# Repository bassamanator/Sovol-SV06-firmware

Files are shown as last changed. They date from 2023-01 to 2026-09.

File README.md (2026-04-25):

<p align="center">
Please consider
<a href="https://ko-fi.com/bassamanator" target="_blank">donating</a> to
support my open source work ❤️
</p>

# One-Stop-Shop Klipper Configuration

| Printer | Branch |
| --- | --- |
| ${\normalsize{\textcolor{darkturquoise}{\text{Sovol SV06}}}}$ | ⚡ ${\scriptsize{\textcolor{darkturquoise}{\text{YOU ARE HERE}}}}$ ⚡ |
| Sovol SV06 SKR-Mini-E3-V3.0 | [skr-mini-e3-v3](https://github.com/bassamanator/Sovol-SV06-firmware/tree/skr-mini-e3-v3) |
| Sovol SV06 Fly-E3-Pro-V3 | [fly-e3-pro-v3](https://github.com/ElPainis/Fly-E3-Pro-v3) \*\* |
| Sovol SV06 Plus | [sv06-plus](https://github.com/bassamanator/Sovol-SV06-firmware/tree/sv06-plus) |
| All other printers | [any-printer](https://github.com/bassamanator/Sovol-SV06-firmware/tree/any-printer) |

${\small{\textit{** Maintained by ElPainis}}}$

> [!WARNING]
> I am creating these files for my personal use and cannot be held responsible for what it might do to your printer. Use at your own risk.

## Outline

- [Features](#features)
- [Stay Up-to-Date](#stay-up-to-date)
- [Preface](#preface)
- [Before You Begin](#before-you-begin)
- [Klipper Installation](#klipper-installation)
  - [Flash Firmware](#flash-firmware)
  - [Download OSS Klipper Configuration](#download-oss-klipper-configuration)
- [Initial Steps](#initial-steps)
  1. [Adjust Configuration with MCU Path](#adjust-configuration-with-mcu-path)
  2. [Configure Your Printer](#configure-your-printer)
- [Adjust Your Slicer](#adjust-your-slicer)
- [Support Me](#support-me)
- [Directory Structure](#directory-structure)
- [Special Considerations](#special-considerations)
- [FAQ](#faq)
- [Useful Resources](#useful-resources)
- [Sovol Official Links](#sovol-official-links)
- [Sources](#sources)

## Features

- 💥 This Klipper configuration is an _endpoint_, meaning that it contains **everything** that you could possibly need in order to have an excellent Klipper experience! 💥
- Filament runout sensor usage implemented.
- Minimum configuration settings for `Mainsail` and `Fluidd`.
- Pre-configured configuration bundles based on the [Ellis SuperSlicer Print Profiles](https://github.com/AndrewEllis93/Ellis-SuperSlicer-Profiles):
  - SuperSlicer
  - PrusaSlicer
  - 🚀 OrcaSlicer 🚀
  - Printer profiles: `SV06/Plus`; `SV07/Plus`
- Bed model and texture to use in SuperSlicer/PrusaSlicer.
- Macros:
  - **Improved** mechanical gantry calibration/`G34` macro that provides the user audio feedback, and time to check the calibration.
  - Misc macros: `PRINT_START`, `CANCEL_PRINT`, `PRINT_END`, `PAUSE`, `RESUME`.
  - Parking macros (parks the printhead at various locations): `PARKFRONT`, `PARKFRONTLOW`, `PARKREAR`, `PARKCENTER`, `PARKBED`.
  - Load/unload filament macros.
  - `PURGE_LINE` macro.
  - `TEST_SPEED` macro. Find instructions [here](#how-do-i-use-the-test_speed-macro).
- Klipper Adaptive Meshing & Purging (KAMP) integrated. Read about it [here](#what-do-i-need-to-know-about-kamp).

[🔼 Back to top](#outline)

## Stay Up-to-Date

${\normalsize{\textcolor{goldenrod}{\texttt{Star ⭐ this project.}}}}$

Watch for [updates](https://github.com/bassamanator/Sovol-SV06-firmware/discussions/37).

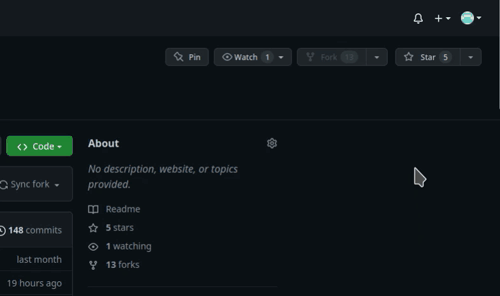
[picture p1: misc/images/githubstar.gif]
github star


[🔼 Back to top](#outline)

## Preface

Although I've made switching over to Klipper as easy as is possible, it can still be a challenge for some, especially considering that most of you have likely never used GNU+Linux. Save yourself the frustration, and fully read this documentation. Also note that Klipper is not a _must_, and is not for everyone. You can stick with Marlin, and have a fine 3D printing experience.

In many ways, this entire repository can be considered _my opinion_ on the `3D printing experience` and this has been _my attempt_ to share that experience. Some factors, such as _accuracy_ and _testing_, have been at the forefront of my thoughts during this process. I hope you find this repository suitable. Cheers.

[🔼 Back to top](#outline)

## Before You Begin

- This entire page is a **9 minute read**. Save yourself _hours of troubleshooting_ and read this documentation fully.
- Follow the steps in order. If an error was reported at a step, do no proceed to the next step.
- It is assumed that you are connected to your host Raspberry Pi (or other host device) via SSH, and that your printer motherboard is connected to the host via a _data_ USB cable.
- It is also assumed that the username on the host device is `pi`. If that is not the case, edit `moonraker.conf` and `cfgs/misc-macros.cfg` to change any mentions of `/home/pi` to `/home/yourUserName`.
- Klipper _must_ be installed on the host beforehand. Easiest is to use [MainsailOS](https://github.com/mainsail-crew/mainsail/releases/latest). [KIAUH](https://github.com/th33xitus/kiauh) is another option.
- Klipper _must_ be up to date.
  - In `Fluidd`, you can do this from `Settings` > `Software Updates`.
  - In `Mainsail`, you can do this from `Machine` > `Update Manager`.
- Robert Redford's performance in _Spy Game (2001)_ was superb!
- It is assumed that there is one instance of Klipper installed. If that is not the case, the steps in this guide will not work _perfectly_ for you.
- Your question has probably been answered already, but if it hasn't, please post in the [Discussion](https://github.com/bassamanator/Sovol-SV06-firmware/discussions) section.
- I would recommend searching for the word `NOTE` in this configuration. There are roughly half a dozen short points amongst the various files that you should be aware of.
- Consider [these](https://github.com/bassamanator/everything-sovol-sv06/blob/main/parts/README.md#printed-upgrades) printable parts, and also see my [Printables](https://www.printables.com/@bassamanator) page.

> [!TIP]
> Most of the micro USB cables that you find at home are _unlikely_ to be data cables, and it is not possible to tell just by looking.

> [!CAUTION]
> Make sure your printer is in good physical condition, because print and travel speeds will be _a lot faster_. Beginners would be wise to run through [these steps](https://github.com/bassamanator/everything-sovol-sv06/blob/main/initialsteps.md).

> [!CAUTION]
> [Disable](https://github.com/bassamanator/everything-sovol-sv06/blob/main/howto.md#disable-usb-cable-5v-pin) the USB cable's 5V pin.

[🔼 Back to top](#outline)

## Klipper Installation

### Flash Firmware

💡 If you flashed Klipper onto your motherboard in the past, you can skip this step.

Please note:

- For the sake of simplicity, I will refer to the firmware file as `klipper.bin` even though the actual filename is something along the lines of `klipper-v0.11.0-148-g52f4e20c.bin`.
- The firmware file is located in the `misc` folder.
- Flashing will only work if current firmware filename is _different from previous flashing procedure_. The `.bin` is also important.
- You may find this [video](https://youtu.be/p6l253OJa34) useful.

> [!WARNING]
> Many users have reported having issues flashing Klipper using the Sovol microSD card.

#### 1. Prepare the microSD Card for Flashing with These Parameters

- Size: `16GB` maximum.
- File system: `FAT32`.
- Allocation unit size: `4096 bytes`.
- Must not contain any files _except_ the firmware file.

#### 2. Flashing Procedure

1. Disconnect any USB cables that might be connected to the motherboard.
2. Copy `klipper.bin` to the microSD card.
3. Make sure the printer is off.
4. Insert the microSD card into printer.
5. Turn on the printer and wait a minute (usually takes 10 seconds).
6. Turn off the printer and remove the microSD.

> [!IMPORTANT]
> ⏲️ At this point, it's not possible to tell with certainty whether your flash was successful, continue on with the guide.

[🔼 Back to top](#outline)

### Download OSS Klipper Configuration

#### Method 1: Clone the Repository

💡 Make sure `git` is installed (`sudo apt update && sudo apt install git`).

1. `ssh` into the Klipper host.
2. `cd ~/printer_data/config`
3. Empty entire `~/printer_data/config` folder.
   - In linux, you can delete files via `rm fileName` and directories via `rmdir directoryName`.
   - In linux, you can list files and folders via `ls -lah`.
4. `git clone -b master --single-branch https://github.com/bassamanator/Sovol-SV06-firmware.git .` ⚠️ Don't miss the period!

#### Method 2: Download the ZIP

1. [Download](https://github.com/bassamanator/Sovol-SV06-firmware/archive/refs/heads/master.zip) the `ZIP` file containing the Klipper configuration.
2. See `Step 2` in `Method 1`.
3. The parent folder in the `ZIP` is `Sovol-SV06-firmware-master`. This is relevant in the next step.
4. Extract **only** the _contents_ of the parent folder into `~/printer_data/config`.

[🔼 Back to top](#outline)

## Initial Steps

### Adjust Configuration with MCU Path

💡 Make sure the host and printer are connected via USB.

1. Find what port the `mcu` (printer motherboard) is connected to via _one_ of the following commands:

   - `ls /dev/serial/by-id/*`
   - `ls /dev/serial/by-path/*`

   1. The output will be something along the lines of
      - `/dev/serial/by-id/usb-1a86_USB2.0-Serial-if00-port0`

2. Adjust the `[mcu]` section in `printer.cfg` accordingly.

   ```yaml
   # 📝 This is just an example
   [mcu]
   serial: /dev/serial/by-id/usb-1a86_USB2.0-Serial-if00-port0
   restart_method: command
   ```

3. Do a `FIRMWARE_RESTART` in the Klipper console.

If the Klipper flash that you did earlier was successful, and you've done everything else correctly, you should see no errors or warnings in the `Mainsail`/`Fluidd` dashboard. 🎉 **Your printer has been Klipperized!** 🎉

[🔼 Back to top](#outline)

### Configure Your Printer

❗☠️ **Your finger should be on the power switch for most of these steps** ☠️❗

❗☠️ **Power off if there is a collision/problem** ☠️❗

💡 The ${\small{\textcolor{red}{\texttt{EMERGENCY STOP}}}}$ button in your dashboard works faster than hitting the power switch.

💡 Do a practice emergency stop.

💡 I recommend no filament be loaded for any of these steps.

> [!NOTE]
> You will be pasting/typing these commands into the `Mainsail`/`Fluidd` console.

1. Check to see if `X` and `Y` max positions can be reached, and adjust `position_max`, if necessary. You might be able to go further, which is great, but I recommend leaving a 2mm gap for safety.
   1. `G28`
   2. `G90`
   3. `G1 X223 F3000`
   4. `G1 Y223 F3000`
2. Do a mechanical gantry calibration; `G34`. After the controlled collision against the beam at the top, there will be a 10 second pause for you to verify that both sides of the gantry are pressed up against the `stoppers` at the top. You will hear a succession of beeps.
   1. Figure out your `Z` `position_max` by baby stepping your way up to the beam, and adjust `position_max`, if necessary.
3. PID tune the bed. Ideally, all PID tuning should occur at the temperatures that you print most at.
   1. `PID_TEST_BED TEMP=70`
   2. `SAVE_CONFIG` (once completed)
4. PID tune the extruder while part cooling fan runs at 25%.
   1. `PID_TEST_HOTEND TEMP=245`
   2. `SAVE_CONFIG` (once completed)
5. Adjust `z_offset`. Make sure your nozzle if very clean. Do the [Paper test](https://www.klipper3d.org/Bed_Level.html?h=probe_calibrate#the-paper-test).
   1. `DO_PROBE_CALIBRATE`
   2. Follow `z_offset` setup in `Mainsail`/`Fluidd`.
   3. `SAVE_CONFIG` (once completed)
6. Create a bed mesh.
   1. `DO_CREATE_MESH`
   2. `SAVE_CONFIG` (once completed)

🏁 If you've made it here, then your Klipperized printer is ready to print! 🏁

_But first_, adjust your slicer.

[🔼 Back to top](#outline)

## Adjust Your Slicer

> [!NOTE]
> If you are using the slicer bundles found on this repo, you can skip this section.

### Start G-Code

It varies depending on your slicer. Find instructions [here](https://ellis3dp.com/Print-Tuning-Guide/articles/passing_slicer_variables.html#slicer-start-g-code).

### End G-Code

```
PRINT_END
```

### Line Purge

If you would like to print a purge line before your print starts, at the end of your start gcode, on a new line, add one of the following:

- `PURGE_LINE`; prints a standard purge line.
- `KAMP_LINE_PURGE`; prints KAMP's purge line.

> [!WARNING]
> Do not attempt to use `KAMP_LINE_PURGE` without reading [this section](#what-do-i-need-to-know-about-kamp).

```yaml
# 📝 This is just an example Start G-Code
PRINT_START ...
PURGE_LINE
```

[🔼 Back to top](#outline)

## Support Me

Please ⭐ star this repository!

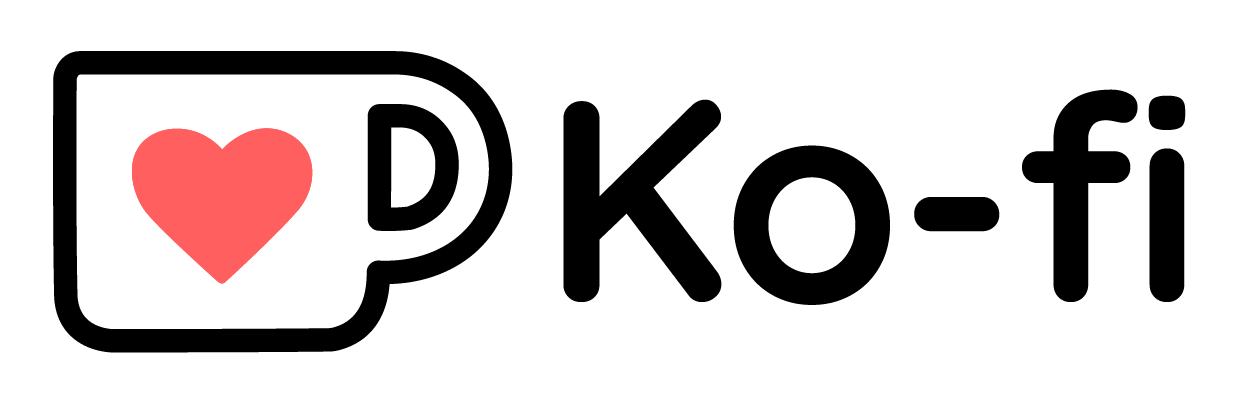
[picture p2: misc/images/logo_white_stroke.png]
Ko-fi
Support [open source](https://en.wikipedia.org/wiki/Open_source), and buy me a [](https://ko-fi.com/bassamanator).

[🔼 Back to top](#outline)

## Directory Structure

This repository contains many files and folders. Some are _necessary_ for this Klipper configuration to work, others are not.

- **Necessary** items are marked with a ✅.
- Items that can _optionally_ be deleted are marked with a 💠.
<!-- tree -a -C -I '.directory' -L 1 -F -->

```sh
/home/pi/printer_data/config
├── cfgs/ ✅
├── CODE_OF_CONDUCT.md 💠
├── CONTRIBUTING.md 💠
├── .git/ ✅❔
├── .github/ 💠
├── .gitignore ✅❔
├── LICENSE 💠
├── misc/ 💠
├── moonraker.conf ✅
├── osskc.cfg ✅
├── printer.cfg ✅
├── README.md 💠
├── SECURITY.md 💠
└── .vscode/ 💠
```

[🔼 Back to top](#outline)

## Special Considerations

### Sequential printing

If enabled, cancelling, or resuming a print from pause, could lead to collisions with previously printed objects. In order to prevent collisions, in your slicer, ensure that objects are printed from the back of the build plate to the front.

In PrusaSlicer, please see Printer Settings > Notes, for extruder clearances.

### Errors

#### MCU 'mcu' shutdown: Timer too close

This error often occurs when the `mcu` is unable to generate the required `microsteps`. Lower power Klipper hosts might be especially susceptible. Reducing `microsteps` to `64`, or even `32` can resolve the issue.

[🔼 Back to top](#outline)

## FAQ

### What are some settings that I can change?

Edit the relevant file according to your needs.

| File | Section |
| --- | --- |
| `cfgs/misc-macros.cfg` | `[gcode_macro _globals]` |

| Variable | Disable | Enable | Notes |
| --- | --- | --- | --- |
| `variable_beeping_enabled` | `0` | `1` (default)  |
| `variable_filament_sensor_enabled` | `0` (default) | `1` |
| `variable_kamp_enable` | `0` (default) | `1` | See [here](#what-do-i-need-to-know-about-kamp) |
| `variable_bed_temp_over` | `0` | `10` (default) | Speeds up print start |
| `variable_bed_temp_not_exact` | `0` | `1` (default)  | Speeds up print start |

### Any differences between this configuration and Sovol's Marlin firmware?

| Property | Marlin | OSS Klipper Config |
| --- | --- | --- |
| `stepper_z` `run_current` | 0.800  | 0.900 |
| `microsteps` | 16 | 128 |

### How do I import a configuration bundle into SuperSlicer/PrusaSlicer?

Please see this [discussion](https://github.com/bassamanator/Sovol-SV06-firmware/discussions/13).

### How do I print using SuperSlicer/PrusaSlicer?

Please see this [discussion](https://github.com/bassamanator/Sovol-SV06-firmware/discussions/14).

### When does beeping occur?

The printer will beep upon:

- Filament runout.
- Filament change/`M600`.
- Upon `PRINT_END`.
- `MECHANICAL_GANTRY_CALIBRATION`/`G34`.

### I want to use a filament sensor. How do I set it up?

You can find information about the physical setup [here](https://github.com/bassamanator/everything-sovol-sv06#filament-sensor).

You can test the sensor via `QUERY_FILAMENT_SENSOR SENSOR=filament_sensor`.

### My filament runout sensor works, but I just started a print without any filament loaded. What gives?

A simple runout sensor can only detect a change in state. So, if you start a print without filament loaded, the printer will not know that there is no filament loaded. You should test your sensor by having filament loaded, starting a print, then cutting the filament. The expected behaviour is that the print will pause, and as long as you have beeping enabled, you will hear 3 annoying beeps.

### What happens when I put in `M600`/colour change at a certain layer?

1. The printer will beep 3 times (not annoyingly).
2. Printing will stop.
3. The printhead will park itself front center.
4. The hotend will turn off, but the bed will remain hot.

### What happens when I pause a print?

Same behaviour as `M600`/colour change _except_ there won't be any beeping.

### What happens when filament runs out?

_If_ you have a working filament sensor, the same behaviour as `M600`/colour change will occur _except_ the beeps will be fairly annoying.

### How do I resume a print after a colour change or filament runout?

> [!WARNING]
> Do not disable the stepper motors during this process!

The printhead is now parked front center waiting for you to insert filament. You will:

1. Heat up the hotend to the desired temperature.
   - Use your Klipper dashboard.
2. Purge (push) some filament through the nozzle.
   - Use your Klipper dashboard, and extrude maybe 50mm (for a colour change you probably want to extrude more).
   - OR, you can push some filament by hand _making sure to first disengage the extruder's spring loaded arm_.
3. Hit resume in your Klipper dashboard.

### What do I need to know about KAMP?

> [!WARNING]
> No KAMP functionality can be used on low-powered devices such as the Raspberry Pi Zero.

> [!WARNING]
> If KAMP is disabled, and there is no `default` mesh, `PRINT_START` will crash.

> [!IMPORTANT]
> The [Label objects setting](https://docs.mainsail.xyz/overview/features/exclude-objects#enable-the-label-objects-setting-in-your-slicer) in your slicer must be enabled for KAMP to work.

> [!NOTE]
> `KAMP_LINE_PURGE` is useable _on appropriate devices_ even if KAMP is disabled.

This repo contains all the code from the KAMP repository, however, only the `adaptive meshing` and `KAMP_LINE_PURGE` functionality of KAMP has been configured and tested for use. To enable other functionality, adjust `/cfgs/kamp/KAMP_Settings.cfg`.

Read [KAMP official docs](https://github.com/kyleisah/Klipper-Adaptive-Meshing-Purging) to learn more.

### How do I use the `TEST_SPEED` macro?

> [!WARNING]
> This is for advanced users only, with well oiled machines. You can cause serious damage to your printer if you're not careful.

Find full instructions [here](https://ellis3dp.com/Print-Tuning-Guide/articles/determining_max_speeds_accels.html).

Some tips:

- Before running with `ITERATIONS=40` with an untested speed/accel value, run with `ITERATIONS=1`.
- Pay close attention throughout the run, so that you can click ${\small{\textcolor{red}{\texttt{EMERGENCY STOP}}}}$ at a moment's notice.
- This macro will simply help you determine the maximum speed your printhead and bed can reliably move at, not necessarily print at. The bottleneck for my SV06, for example, is the 15mm/s^2 that the hotend maxes out at (well under 200mm/s actual print speed).

### How do I compile my own firmware?

Please see this [discussion](https://github.com/bassamanator/Sovol-SV06-firmware/discussions/111).

[🔼 Back to top](#outline)

## Useful Resources

- [Everything Sovol SV06](https://github.com/bassamanator/everything-sovol-sv06)
- [RP2040-Zero ADXL345 Connection Klipper](https://github.com/bassamanator/rp2040-zero-adxl345-klipper)
- ⭐⭐⭐⭐⭐ [Ellis' Print Tuning Guide](https://ellis3dp.com/Print-Tuning-Guide)
- [Simplify3D Print Quality Troubleshooting Guide](https://www.simplify3d.com/resources/print-quality-troubleshooting/)

[🔼 Back to top](#outline)

## Sovol Official Links

- [SV06 Marlin Source Code](https://github.com/Sovol3d/Sv06-Source-Code)
- [SV06 Models](https://github.com/Sovol3d/SV06-Fully-Open-Source)
- [SV06 Plus Marlin Source Code and Models](https://github.com/Sovol3d/SV06-PLUS)

[🔼 Back to top](#outline)

## Sources

- [https://www.klipper3d.org](https://www.klipper3d.org)
- [Ellis' Print Tuning Guide](https://ellis3dp.com/Print-Tuning-Guide)
- [Mechanical Gantry Calibration Macro](https://github.com/strayr/strayr-k-macros)
- [SV06 printer.cfg](https://github.com/spinixguy/Sovol-SV06-firmware)
- [SV06 Buildplate and Texture](https://www.printables.com/model/378915-sovol-sv06-buildplate-texture-and-model-for-prusas)
- [Ellis' SuperSlicer Profiles](https://github.com/AndrewEllis93/Ellis-SuperSlicer-Profiles)
- [Klipper Adaptive Meshing & Purging](https://github.com/kyleisah/Klipper-Adaptive-Meshing-Purging)
- [PrusaSlicer Print Settings](https://github.com/mjonuschat/PrusaSlicer-Profiles)



[🔼 Back to top](#outline)

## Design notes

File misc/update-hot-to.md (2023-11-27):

\*\* _Flashing the firmware is not required for any method_

## Should You Update?

I treat this config like software, and like any piece of modern software, it will require periodic updates to fix issues, add features, improve functionality, etc. So, if you want to have the latest and greatest, I recommend you periodically pull the changes from this repo.

### What Changes Should You Be Concerned With

The only changes you need to be concerned with relate to the `.cfg` and `.conf` files; all changes to `.md` files (these are markdown files, the text that you see when you visit this repo) can be ignored.

### Git Users

If you do a `git diff origin/master --name-only` and it shows you that a `.cfg` file has changed, you might want to pull in those changes (but you don't have to).

### Non-Git Users

Unfortunately, there's no simple way for you to ascertain whether there have been changes. I simply recommend that you update your config via the instructions below from time to time.

## Hot to Update

There are three methods to accomplish this:

1. The correct method, using `git`.
2. The mostly acceptable method, without using `git`.
3. The start-from-scratch method. _Recommended for non-git users and those who haven't made many changes to their configuration._

### The `git` method.

⚠️ This method is only intended for those who already know how to use `git`.

🗒️ In this example, I'm using the `master` branch which applies to SV06 users only. Be sure to use the appropriate branch for your printer.

🗒️ The assumption is that you didn't change branches after the initial setup, so you are in `master`, and there are many untracked changes.

1. `ssh` into your Klipper host.
2. `cd ~/printer_data/config`
3. `git checkout -b my-settings`
4. `git add .`
5. `git commit -m "Saving my settings."`
6. `git checkout master`
7. `git pull`
8. `git checkout my-settings`
9. `git merge master --no-ff --no-commit`
10. Deal with comparing and pulling in incoming changes from `master` using your favourite code editor. You can also do this from the command line via `git commit --interactive`, however, only advanced `git` users should attempt this, though it is easy enough.
11. Add all welcomed changes to the staging area, and discard all other changes.
12. `git commit -m "Update with upstream."`

You should push your branch to your own fork of this repo.

For any future updates, you can run through the same process again, however, you cannot re-create the `my-settings` branch as you did in `step 3`, because it already exists. Simply omit the `-b` flag in `step 3` next time you update.

### The mostly acceptable method.

This method has shortcomings, because it relies on the user's memory, and requires more manual edits. Perfectly functional method, however.

1. Read all the documentation.
2. Backup your current configuration, essentially everything inside `~/printer_data/config`.
3. Repeat steps in [Download OSS Klipper Configuration](https://github.com/bassamanator/Sovol-SV06-firmware#download-oss-klipper-configuration), and [Adjust Configuration with MCU Path](https://github.com/bassamanator/Sovol-SV06-firmware#adjust-configuration-with-mcu-path).
4. Copy everything from `#*# <---------------------- SAVE_CONFIG ---------------------->` onward and paste into new `printer.cfg`, inclusive.
5. Copy any other changes you might have made into the new configuration. Maybe you had adjusted the size of your printer (`position_max`), or other such changes.

### The start-from-scratch method.

1. Delete the folder `~/printer_data/config`.
2. Recreate the folder `~/printer_data/config` via `mkdir ~/printer_data/config`.
3. Start the Klipper installation process starting from `Download OSS Klipper Configuration` in the appropriate branch.

## Linux Tips

- In linux, you can delete files via `rm fileName` and directories via `rmdir directoryName`.
- In linux, you can list files and folders via `ls -lah`.

You are now up-to-date with this repo, and have added your personal settings on top.

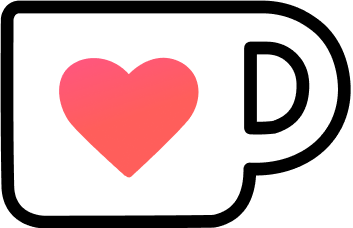
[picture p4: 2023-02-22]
misc/images/cup-border.png

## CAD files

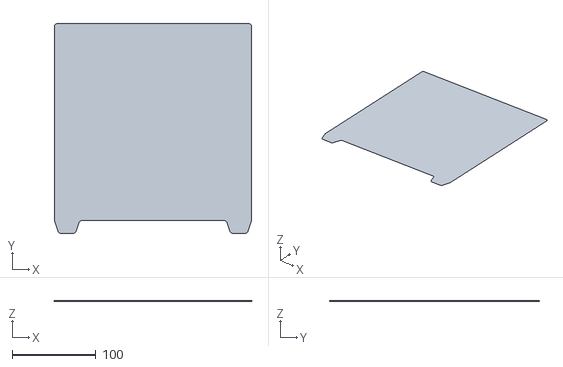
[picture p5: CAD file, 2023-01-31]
misc/SV06-buildPlate.stl
235.0 x 250.0 x 0.4

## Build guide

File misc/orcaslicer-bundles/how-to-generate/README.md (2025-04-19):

## Converting PrusaSlicer/SuperSlicer config bundles to OrcaSlicer

OrcaSlicer configs can be converted from PrusaSlicer using [SuperSlicer_to_Orca_scripts](https://github.com/apparle/SuperSlicer_to_Orca_scripts). It is a fork of theophile's script with some enhancements which haven't been merged yet ([theophile/SuperSlicer_to_Orca_scripts#43](https://github.com/theophile/SuperSlicer_to_Orca_scripts/pull/43)). It does require a few perl modules which can be installed using `cpanminus` (or your favorite perl module manager).

Most of the script is automated, with the exception of `printer_model` field which must be manually specified with a `json`. This attribute is used by OrcaSlicer to load the appropriate build plate images & STLs.

```
perl SuperSlicer_to_Orca_scripts/superslicer_to_orca.pl --input PrusaSlicer_config_bundle-2.9.2.ini --nozzle-size 0.4 --compatible_printers_condition KEEP --skip-link-system-printer --printer-models-json printer_models_conversion_mapping.json --output-config-bundle OrcaSlicer_config_bundle-2.9.2-DEV.zip
```

## How to use OrcaSlicer bundle:

This config bundle can be imported into OrcaSlicer : `File > Import > Import configs...`

Note, OrcaSlicer reformats the `json` and adds some default attributes, so the imported files cannot be directly compared with the contents of the zipped bundle. But you can use json comparison tools like [https://www.jsondiff.com/](https://www.jsondiff.com/) to analyze the differences if needed.

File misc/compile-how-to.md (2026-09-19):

${\small{\textcolor{green}{\texttt{2 minute read}}}}$

# Everything about `klipper.Bin` for the SV06/Plus

## FAQs

### Do I need to re-flash the motherboard?

You will _almost never_ need to re-flash your motherboard. When this is needed, your dashboard will explicitly tell you that you need to re-flash.

### Where does Klipper live?

1. On the motherboard.
2. On the host device (Raspberry Pi, etc.).

🗒️ These 2 versions of klipper can rightly differ.

### Should I update Klipper, moonraker, etc.?

I always update everything on the host device via the dashboard. I don't want to miss out on improvements, especially those that improve safety. What this means is that on some occasions, there will be breaking changes: you will need to change a few things in your config **before you can print**. I would suggest that if you absolutely have to get something printed immediately, and there's an update, perhaps wait till after the print completes to do the update.

Others will argue that "if it ain't broke, don't fix it".

You have to decide what camp you want to be apart off.

#### How-To

- In `Fluidd`, you can do this from `Settings` > `Software Updates`.
- In `Mainsail`, you can do this from `Machine` > `Update Manager`.

## Compilation Steps

### SV06/Plus

1. `ssh` into the Klipper host (i.e., RPi, OrangePi, etc.).
2. `cd ~/klipper`
3. `git pull`
    - Pulls the latest changes from the klipper repo, ensuring that your `klipper.bin` will be as fresh as possible.
4. `make menuconfig`
5. Set things up to look as follows:

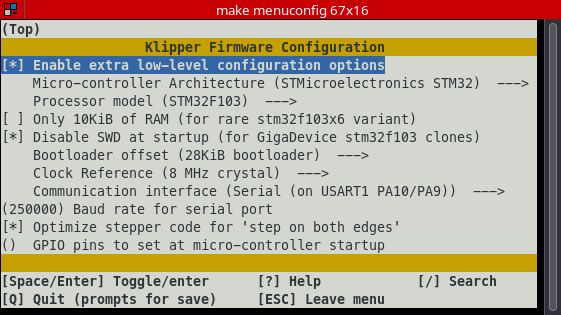
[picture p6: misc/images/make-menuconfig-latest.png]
make-menuconfig
    
6. `make clean`
    - Clears `~/klipper/out/`
7. `make`
    - Compiles `klipper.bin` and puts it in `~/klipper/out/`

### SKR-MINI-E3-V3

Follow the same steps as above except set things up to look as follows:

make-menuconfig
[Source](https://github.com/bigtreetech/BIGTREETECH-SKR-mini-E3/tree/master/firmware/V3.0/Klipper)

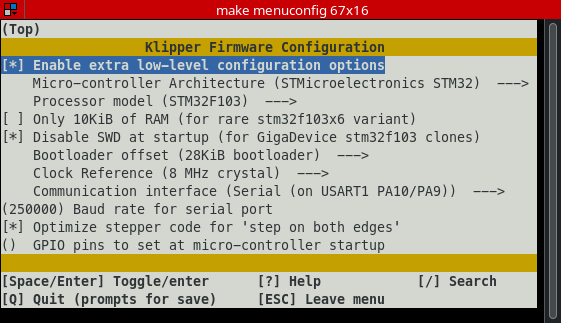
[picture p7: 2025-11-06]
misc/images/make-menuconfig-v0.13.0-371-g7a723bdc.png

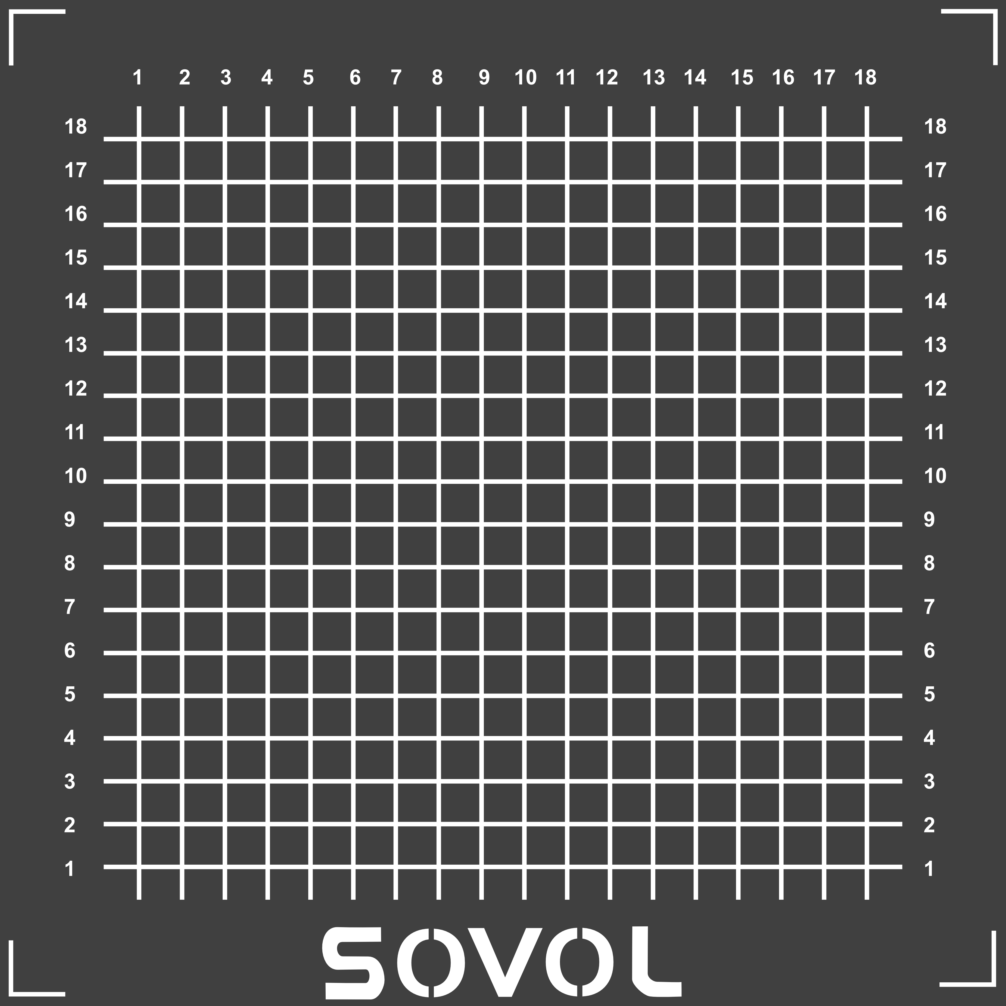
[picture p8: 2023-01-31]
misc/sv06-buildPlate.png

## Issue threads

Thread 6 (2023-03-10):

Print Cancel Issues

s3anami, 2023-03-10:
I am using this firmware on my Creality Sonic Pad, and occasionally have issues with print cancellations. Occasionally when I cancel a print it doesn't truly fully cancel it. For example, I can the print, cancel it on the pad, clear the bed and attempt to reprint, the printer will attempt to resume printing instead of restarting for some reason. I have to power cycle the printer to clear it.

Another issue I had were the mesh point settings. They were also off for me compared to the official and some other cfg set ups ( too low on the build plate, y value too low, and x values too low as well).

bassamanator, 2023-03-10:
Although I haven't made any changes to any of these macros recently, are you up to date with this repo? I cancelled some prints just yesterday and didn't have any issues.

I don't know what the sonic pad does. Can you start and cancel the print using the Mainsail or Fluidd interface?

bassamanator, 2023-03-10:
> Another issue I had were the mesh point settings. They were also off for me compared to the official and some other cfg set ups ( too low on the build plate, y value too low, and x values too low as well).

I don't follow you here, please elaborate. You need to adjust your z_offset as well, this is all very clearly explained in the `Initial Steps` section.

s3anami, 2023-03-10:
yup i did, i was commenting on the default values, don't need to be rude. Good

Closed 2023-03-10.

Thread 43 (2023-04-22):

[BUG] No purge line SV06 Plus?

LsHallo, 2023-04-22:
**Describe the bug**
When using the PRINT_START and PRINT_END macro no purge line is printed resulting in inconsistent first layers.

**To Reproduce**
1. Set Cura pre-print to "PRINT_START"
2. Set Cura post-print to "PRINT_END"
3. Print the sliced G-Code
4. Observe that no form of purge line is printed before starting the print.

**Expected behavior**
I would expect the macro to print the purge line. This line would be in the cura pre-print code previously but with Klipper it is common practice to replace the whole pre-print block with just "PRINT_START".

**Screenshots**
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

**What kind of device are you using to host Klipper?**
 - OS: Debian @ BigTreeTech CB1
 - Version: Klipper 011b4e3

**How did you install Klipper?**
 - KIAUH

bassamanator, 2023-04-22:
Change your Cura start code as follows:
```
PRINT_START BED={material_bed_temperature_layer_0} HOTEND={material_print_temperature_layer_0} CHAMBER={build_volume_temperature}
PURGE_LINE
```

bassamanator, 2023-04-22:
Re-open if the need arises.

Closed 2023-04-22.

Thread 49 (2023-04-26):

Cannot seem to get this method working? please help, where am I going wrong?

MisteroUK, 2023-04-26:
Hi,

So I am trying to get this to work with my sv06, SKR mini E3 V3 and im struggling at the section labelled "Download Klipper Configuration"

The firmware flashed fine, I installed a mainsail klipper image onto a raspberry pi via pi manager but unfortunately this is as far as I can get things working.

Your instructions under "Download Klipper Configuration" say to delete everything in the ~/printer_data/config folder which I have done but the files you're suggesting to download don't match up?

you said to put everything from the folder "Sovol-SV06-firmware-master" into the now empty ~/printer_data/config folder but with the download there is no folder named "Sovol-SV06-firmware-master". If im honest I have no idea what this folder should look like or hold so any help for a newbie to klipper would be really helpful.

If you could give a newbie / simple terms of exactly what should be in that folder would be great as every time I try it ..... everything breaks and nothing will work? klipper goes off line and won't start.

Thanks

Steve

bassamanator, 2023-04-26:
I've edited the instructions. Please try again, [skr-mini-e3-v3](https://github.com/bassamanator/Sovol-SV06-firmware/tree/skr-mini-e3-v3).

Keep updating this thread.

MisteroUK, 2023-04-26:
Thank you ;-) so just to get this right you delete everything out the config folder including the link directories and then copy the entire contents of the git folder download in this config folder? I know im a newbie to klipper but there are a lot of files and folders in there that don't seem relevant?

Im sure im missing something here but its still not making sense lol.

bassamanator, 2023-04-26:
That's right, everything inside `~/printer_data/config`.

The skr branch is not as robust with the instructions because I have yet to install mine. The master branch on the other hand has been tried and tested countless times, have faith in those instructions.

bassamanator, 2023-04-26:
It costs nothing to try again, start again [Download Klipper Configuration](https://github.com/bassamanator/Sovol-SV06-firmware/tree/skr-mini-e3-v3#download-klipper-configuration).

Follow and read the steps exactly.

bassamanator, 2023-04-26:
Also, you mentioned git earlier for some reason, if you're downloading the zip, then git is not at play.

MisteroUK, 2023-04-26:
I am downloading the zip as mentioned then uploading the entire contents of that but the printer is def not performing as it should, hot end crashes into the bed, y axis doesn't homeless sense (jumpers are installed on the board) I stopped at this point as the printer was going to get damaged. looks like the config isn't working or being read correctly.

bassamanator, 2023-04-26:
A `firmware_restart` is required after you edit `printer.cfg`. Try that, or the mainsail option does the same thing.

The enclosure fan behaviour can be changed, should turn off after 60 seconds.

MisteroUK, 2023-04-26:
tried it but for some reason its still not working? very strange, now y axis has completely died and will not respond at all... oh dear :-(

MisteroUK, 2023-04-26:
tried many re starts but totally dead

MisteroUK, 2023-04-26:
ok PB14 on the y needed an ! in front so that's back but not working as should. Both the x and y are now both moving on a g28 but only one step

MisteroUK, 2023-04-26:
Strangely a g28 sends everything in the wrong direction ????? im getting confused now lol

bassamanator, 2023-04-26:
The homing sensitivity is too high, that's why it stops after a slight move.

Change both `driver_SGTHRS: 81`.

MisteroUK, 2023-04-26:
bingo!!!!!

ok we got a successful home. one question. when the home has finnished it sounds like the motors are locked and possibly under some form of resistance as they are getting hot and buzzing just idle. If I do an M84 this releases them and they go silent and cool down. Any ideas?

bassamanator, 2023-04-26:
Well they won't be *getting* hot, unless you've change the current. Do me a favour and paste a picture of the back of the x stepper, the amperage is listed there. In any case, the steppers are engaged because the printer has homed, and needs to know where the nozzle is.

Also please attach the `printer.cfg` to your next message, you might have to rename to .txt. Please also star the repo if you haven't already.

MisteroUK, 2023-04-26:
1.3a on the back of the motor

I will grab the printer config in a sec and send over

MisteroUK, 2023-04-26:
[printer.txt](https://github.com/bassamanator/Sovol-SV06-firmware/files/11337109/printer.txt)

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

MisteroUK, 2023-04-26:
The motors got REALLY hot while locked in doing a bed PID

bassamanator, 2023-04-26:
K same as mine and everyone else (except the first batch I believe).

Stepper motors are rated at ~125C. In any case, feel free to lower the current. Keep in mind, however, that the run_current is pulled from Sovol official marlin settings.

☢ Having said all that, the motors should not be getting this hot, whatever that means. You might have a wiring issue here. Proceed with caution.

MisteroUK, 2023-04-26:
hmmm doesn't sound good :-( they were working absolutely fine and not getting hot at all with the original set up. Now they are roasting, really hot!!! doesn't sound safe at all with this set up, and I got so close.

bassamanator, 2023-04-26:
Turn off the printer now.

Are they all getting hot? Let me see the `printer.cfg`.

bassamanator, 2023-04-26:
Any which steppers are getting hot?

MisteroUK, 2023-04-26:
all of them

MisteroUK, 2023-04-26:
and they are whining

MisteroUK, 2023-04-26:
[printer.txt](https://github.com/bassamanator/Sovol-SV06-firmware/files/11337413/printer.txt)

bassamanator, 2023-04-26:
The printer.cfg looks fine, although I didn't see any changes to the `dir_pin`, are you sure this is the correct one?

As long as you feel that there are no wiring issues, you can do the following.
- Cut down `run_current` by half on all steppers that are getting hot.
- If they feel only warm to the touch, try printing something.
- If the print succeeds, you've good to go.
- If the print fails, reduce run_current further and print again.
- Repeat until you have a working printer and the steppers aren't getting crazy hot.

Hot is okay btw, sizzling hot is not ok.

MisteroUK, 2023-04-26:
I had the same idea to go down by half on all hot motors so I adjusted them to the following the attached config file below

[printer.txt](https://github.com/bassamanator/Sovol-SV06-firmware/files/11337569/printer.txt)

You will also see I have made some changes to the fan section as well. Let me know what you think :-)

Also I am currently using Prusaslicer and have some start and end GCODE im using. It worked fine with the original set up but wondered if you could have a look to see if it will be ok to use with this board and klipper set up?

*****START CODE*****

G90 ; Use absoulte coordinates
M83 ; Extruder relative mode

M220 S100 ; reset feed rate to 100 percent
M221 S100 ; reset flow rate to 100 percent

M900 K0.07 ; Set Linear Advance K Factor

G28 ; Home all axes

M104 S165 ; set extruder temp pre-heat
M140 S[first_layer_bed_temperature] ; set bed temp
M190 S[first_layer_bed_temperature] ; wait for bed temp

M420 S1 ; load abl mesh
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
bassamanator, 2023-04-27:
If possible, try to take a temperature reading of the steppers. I have what I would call a high pain tolerance, however, 65-70C stepper motors are painful to keep in contact with for more than 15 seconds, let's say.

I don't know if the plastic part holding the x stepper motor will survive a 'red hot motor'.

The error might be due to the mcu not being able to generate the required microsteps. If you encounter the error again at the default run_current, you can try reducing all microsteps to 64. Let's have a look at your `System Loads` section under the `Machine` tab.
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

MisteroUK, 2023-04-27:
this is one screen shot of the system idle......... I will wait for it to cool, set up another print and screen shot it while printing as well.

I also have a digital thermometer laser gun on order, should be here tomorrow so I can get some factual readings rather than just me feeling the motors.

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

bassamanator, 2023-04-27:
I would recommend reducing microsteps given that this mcu is a bit slower, won't affect much, if anything at all.

MisteroUK, 2023-04-27:
Here is a screen shot of the system loads while running a print. I haven't seen the MCU go above 12% at all and that is with 128 microsteps setting

One thing I will say is that the drivers on this board are the noisiest I've heard yet, sounds like an old pc game loading on tape lol.

Any adjustments to quieten them down at all do you know?

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

bassamanator, 2023-04-27:
The load has nothing to do with it.

At microsteps 64 or greater, things are as quiet as can be. You can turn on stealthchop to quiet things further, check klipper docs.

The klipper firmware, provided by BTT themselves, is quite old now from what I see in the picture, usually it's not an issue. Having said that, I would suggest you recompile it yourself according to docs found on the skr branch. It may help with your hot steppers.

MisteroUK, 2023-04-27:
Now that was my next thought so I think that is what I will be doing next :-)

I dropped the X anY to current values of 0.7 and the z at 0.8 and they are all at a reasonable temp for now.

inorichi, 2023-04-28:
I'm having the same issue, the steppers are whining until they are unlocked and they get really hot. I've been using the printer (the plus one) with the stock firmware for two weeks and they didn't ever make that noise. I don't know if they will degrade quickly like this.

I dumped the Marlin settings before switching and I can confirm the current values are correct on all steppers in your cfg so I think it should be something else (this is my first printer so I don't really know where the issue is).

I didn't make any change/mod to the printer itself btw.

MisteroUK, 2023-04-28:
Hi inorichi,

I think I may have solved this but have some more testing to fully confirm.

Try the following:

Enable stealthchop on the tmc section and adjust the current value to 0.580 on all

should look something like below but remember im still testing so haven't confirmed the final best settings.

if you want to print fast not quiet then don't enable stealthchop.

[tmc2209 stepper_x]
uart_pin: PC11
tx_pin: PC10
run_current: 0.580
stealthchop_threshold: 0
interpolate: False
sense_resistor: 0.150
uart_address: 0
driver_SGTHRS: 81
diag_pin: PC0
stealthchop_threshold: 999999

MisteroUK, 2023-04-28:
Hey Bassam Husain,

Just to let you know I have carried on tuning the profile to get some results for you, I have attached below the printer config so you can have a look as your working on this project.

All in all I have this now printing successfully using prusaslicer using MK3s+ print settings as a base to start with. I have measured all temps of the stepper motors now based on the settings in the config file and all motors run between 35 - 45 degrees celsius.

I dropped the microsteps to 64 to give some head room and enabled stealthchop to quieten it down.

I compiled a new firmware and uploaded as well and now have it running fine with Klipper Screen.

All in all I have to thank you for help with my first steps over from Marlin into the world of Klipper :-)

If there is anything else you would like me to try or change to help then just give me a shout.

Printer Config File:
[printer.txt](https://github.com/bassamanator/Sovol-SV06-firmware/files/11355744/printer.txt)

System:
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

Pictures:

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

bassamanator, 2023-04-29:
@MisteroUK You're welcome.

Your machine is looking sharp. Love the KlipperScreen.

Please attach the newly compiled firmware, if possible.

Please star the repo, and watch for updates. Thanks!

Closed 2023-04-29.

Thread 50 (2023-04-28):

MECHANICAL_GANTRY_CALIBRATION not working properly

MirkoMorello, 2023-04-28:
Hi, I've been trying to use the MECHANICAL_GANTRY_CALIBRATION (G34 code) to calibrate my z axis, the problem is that the command doesn't seem to work correctly, the left motor doesn't push the left hinge of the rail all the way up.
The right part touches the top, after that, the left one pushes a bit towards the top but it doesn't have enough torque to push all the way through and align.
I tried rotating the coupler during the few seconds the steppers go off, but even though I do that, there still is a systematic error since doing another gantry calibration exactly after the first one shows the gap again, even if sometimes lower.
Thinking it was an HW problem, I tried reinstalling Marlin to see if the problem was reproducible with the stock firmware, and it doesn't look like it's the case because the gautry perfectly aligned, both hinges touched the top at the same time (after first calibration). This suggests that the gantry can't be pushed all the way up manually, it needs the motor to do this job correctly in order to perfectly align the two parts of the rack.
I tought I could bypass this problem with a SW solution like a simple bed mesh, but even with bed meshing for some reasons it still causes problems of not uniform distances from the bed while printing, leading to bad first layer adhesion in the right side of the bed.
I know that bad adhesion due to z axis misalignment is a common problem for SV06 users, and that the usual way to approach this is to do a manual calibration putting two identical pieces between the bed and the lower rail of the z axis rack and loosening/tightening the couplers until both of them touches slightly, and this seems to have fixed the problem (bed meshing suggests there is a delta of 0.2/0.3 mm), but it's a shame that I can't use the automatic gantry calibration with klipper since it seems's I'm one of the few lucky people that have a good calibration after a g34 in the stock firmware.
I guess that this is a problem of the MECHANICAL_GANTRY_CALIBRATION code present in the cfg folder, since it's been transposed from a Ender 3 printer implementation of the same feature (most likely) or that there is some tuning problems that led to different full revolution of the z motors (less likely).

bassamanator, 2023-04-29:
I've heavily tested and modified the macro for improved functionality. It works just fine.

Apparently, there have been 2 different kinds of motors that were shipped. *Your* steppers need more current. Even with the same steppers, it's possible for one user having to increase current compared to another user with the same steppers.

The default current set in the macro is `0.2`, increase it very slowly: `MECHANICAL_GANTRY_CALIBRATION CURRENT=0.25`. Be ready to do an emergency stop at a moment's notice.

Make sure you've pulled all the latest changes, and make sure your z couplers are secure.

MirkoMorello, 2023-05-01:
Hi Bassam, to my great pleasure you were right!
Now it aligns perfectly, but it has a little bit of coil whine, I'll try with lower current. By the way, does increasing the current as I did lead to problems on the long run? I personally modified line 69 of the function, putting `SET_TMC_CURRENT STEPPER=stepper_z CURRENT=0.25 ; drop current on Z stepper`, so the current gets from 1.0 to 2.5 (instead of 2.0) for the operation of the gantry calibration, I've tried to understand what `oldhold` is but `hold_current` is not present in the config file.
Unluckily, I found out that the alignment leads to worse calibration than I originally thought, after aligning, the bed mesh has a delta of 0.7mm, which is too high. I don't know why but stock marlin firmware did a better job with bed meshing, must be a little bit more aggressive with the corrections than the one in Klipper.
I'll try to make a shim roughly 0.5/0.7 mm to make the automatic alignment more precise, as of right now I'm stuck with manual calibration, which brings me to a delta of 0.2/0.3 mm, which is more due to normal bed deformation, I'll attach images about the results of manual calibration below.
Last question, how are you doing calibration on your printer? Do you have any suggestions?
Just wanted to say thank you for your work and for being so helpful to everybody, I appreciate it.

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

bassamanator, 2023-05-02:
You're welcome.

Lowering or increasing current during this process is a non-issue. Keep in mind, we're talking 0.0 to 1.0, anything higher could lead to blowing up your motors. You said 2.5 up there...

What was the range with marlin?

Shimming can work, the silicone mod is another option. This model is notorious for x-twist as well.

Try to printing a layer test to see if there really is a problem. Use a filament where the extrusion multiplier is 1.
[parametric_bed_mesh_test_generator-30mm-SovolSV06-extrusion_multiplier1.tar.gz](https://github.com/bassamanator/Sovol-SV06-firmware/files/11369019/parametric_bed_mesh_test_generator-30mm-SovolSV06-extrusion_multiplier1.tar.gz)

MirkoMorello, 2023-05-02:
Apologies, I edited my previous message, I meant to say 0.25
With Marlin I couldn't check the range because you don't have this information, I just saw it had a better first adhesion for a 10/15cm object placed in the center right after the gautry automatic calibration, but I'm starting to blame myself due to poor testing, I should have tried to print something larger like the one you just shared. It definitely looked better than the one with klipper after automatic calibration but I'm lacking information to assess it was perfect, which I honestly don't think it was.
I'm starting to see problem with adhesion at the extreme edges of my prints so I think it could be caused by the x-twist as well, any suggestions for fixing it?

I'll try your test and post about it in a few days, I'm not home and can't test it right now.
I'm new to 3D printing so I've never tested the extrusion multiplier of my filaments, I'll do it as accurate as I can and see if I have one with multiplier to 1.
In case it's not 1, if you can share the stl I'll change the multiplier to the one I'll find and slice it.

iJebus, 2023-05-28:
Not to revive a dead topic, but I feel like my question is related. Running G34 on my SV06 fails, with only one stepper moving for the bump. With steppers off and turning them manually, I notice the stepper not moving is very stiff or crunchy, for lack of a better term. Does that indicate a bigger issue or would you recommend bumping up the current as above, until they both move?

bassamanator, 2023-05-28:
Always good to revive an old thread.

>  With steppers off and turning them manually, I notice the stepper not moving is very stiff or crunchy, for lack of a better term.

Are you saying that the z steppers are always 'unsmooth'? That sounds like the bearings need lubrication. See Savage Lau's video on this. Putting grease on the rods provides the most minor form of lubrication btw.

Having said that, it seems that you're in the same boat as the OP. Follow my instructions to him, always being ready to hit emergency stop during gantry calibration.

iJebus, 2023-05-29:
Haha, so, TLDR, bumping the current to `0.45` worked and gantry ramming works. 🚀

What I was trying to explain is that I noticed while the printer was powered off, manually turning one of the steppers was more difficult. I wondered whether that might indicate some sort of pending mechanical failure. That's getting pretty far outside the scope of this issue though. Thanks for replying and thanks for everything you've put together in this repo!

bassamanator, 2023-05-29:
Great!

For optimal performance, both sides of the motion system should work the same. Check to make sure the z couplers are well tightened though don't over do it. Maybe also check bolts holding the z steppers. I don't think it's a big issue, but something you might want to look into when you have time. Best!

Closed 2023-05-19.

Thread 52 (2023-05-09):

MicroSD that comes with SV06 cannot flash the MCU with Klipper.bin

nickmmain, 2023-05-09:
I'd just like to report that I can confirm exactly the behavior that was reported in:

https://github.com/bassamanator/Sovol-SV06-firmware/discussions/32

I lost a couple hours trying and re-trying to flash the SV06 with Klipper.bin. I had the exact same errors and debugging output.

The solution was also the same; I used a SanDisk 16GB micro SD card, formatted as directed in the Readme. Can, or should, it be mentioned in the readme to **not** use the SD card provided with the machine ?

bassamanator, 2023-05-09:
Interestingly enough, I could *only flash* using the microSD card that came with the printer.

Are you able to flash Marlin using the Sovol sd card (Kingfast I believe)?

JayKayUk, 2023-05-09:
I'll just jump in here and also confirm that the microSD card that came with the printer doesn't work for flashing for me. It worked once for Hill's version of Marlin, but after like 20 power cycles. Some time after that I wanted to flash Klipper, I couldn't flash it nor the 1.9.2 firmware, even after multiple power cycles. I had to buy the SanDisk 16 GB. It literally worked first try.

bassamanator, 2023-05-09:
@JayKayUk Are you saying that you were able to flash Marlin with the Sovol sd card, but not Klipper?

JayKayUk, 2023-05-09:
I'll walk you through what I've done with what:

1. Got the SV06 printer and after some time updated to 2.0.0 with the stock SD card (Kingfast or whatever it is). It took a lot of power cycles and being afraid, I bricked the board.
2. After some time found Hill's updated version of Marlin with UBL and all. Again, flashed it with the stock card with maaaany power cycles.
3. After that, I got interested in Klipper, so I tried flashing it with the stock card. It didn't seem to work, so I thought I'd try to flash 1.9.2 fw. Didn't work either. Said screw it. Now the printer doesn't work at all.
4. Ordered the SanDisk 16 GB from Amazon. Flashed 1.9.2 fw first try. After I confirmed that the board is not bricked from me trying different files/names/power cycles, I tried flashing Klipper. Worked first try again.

bassamanator, 2023-05-09:
@JayKayUk Very interesting. Let's see what @nickmmain has to tell us.

corbt, 2023-05-20:
I'm also using the stock KingFast 8GB SD card and am unable to flash the Klipper firmware. The printer just gets stuck on a blank screen and never boots up.

I am able to flash the stock 2.0.0 firmware using the same card.

bassamanator, 2023-05-20:
@corbt Thanks for the feedback. I'll add a warning to that section.

Closed 2023-05-20.

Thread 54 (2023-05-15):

Screen on SV06 gets messed up on longer prints

Odinios, 2023-05-15:
On longer prints >3 hours, sometimes the screen on the printer bugs out and symbols change / not all info shows up correctly. WebUI  (mainsail) still seems to function properly.

When I was running a webcam the issue was more common and froze the WebUI and eventually the print stopped. Currently not using any webcam.

A firmware restart will fix the issue, just can't do that mid print, also don't want the print to randomly stop...

I have tried changing the USB cable from Raspberry Pi to SV06 and reseated the screen cable.

Below is an image when it messes up. *Does not always look like this, sometimes it's different:
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

If this isn't the right place to post this or if it needs to be removed, let me know (new to GitHub)

bassamanator, 2023-05-15:
This isn't an issue related to the OSS config, but let's try to solve. The screen on this printer is somewhat problematic, I've seen countless posts about it dying, or bugging out worse than what you've posted, so it is probably just that.

What are the specs of the RPi?

Can you also do the mod found [here](https://community.octoprint.org/t/put-tape-on-the-5v-pin-why-and-how/13574)? I'm not saying this will solve your issue, but the RPi is providing *some* power to the printer, which is dangerous regardless, and I wonder if this is potentially causing an issue.

Odinios, 2023-05-15:
Thanks, I'll try that post once the print finishes. It's raspberry  pi 4b 4gb model.

Odinios, 2023-05-15:
I'm gunna give the print another try now, will report back in a few hours. I suspect the pin mod on the cable will solve the issue. Thanks again!

bassamanator, 2023-05-16:
@Odinios So did that work?

Odinios, 2023-05-16:
@bassamanator I ran the print again (with the fix) and it didn't mess up! So I'm assuming it's all fixed

bassamanator, 2023-05-16:
@Odinios Great! 😀

Please star the repo if you found it useful.

Closed 2023-05-16.

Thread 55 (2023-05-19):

[BUG] Z offset is not saved/applied

bladyle, 2023-05-19:
**Describe the bug**
I have installed klipper on old laptop and everything work except I cant see that my z offset is applied when I'm printing.
I have terrible first layer and bed adhesion.
I have done the step for z offset calibration from first page and typed save_config after that. I can see my value on the bottom of the printer.cfg but no on the z offset widget on the dashboard.

**What kind of device are you using to host Klipper?**
 - OS: Linux Mint on Laptop
 - Version: latest

**How did you install Klipper?**
 -KIAUH,

**Additional context**
Add any other context about the problem here.

Value from config file is:
#*# [probe]
#*# z_offset = 1.505
but when I set it up it is negative if that's metter.

bassamanator, 2023-05-19:
You don't have to worry about applying the z offset manually somewhere, as long as you've done a `probe_calibrate`, `save_config`, you're good to go.

The widget displays any babystepping z offset values, it doesn't display your `z_offset` from the `printer.cfg`.

bassamanator, 2023-05-19:
This is not an issue. Please create a Discussion about your bed levelling issues. Unfortunately, you probably suffer from x twist; please see some info about it in the discussions.

bladyle, 2023-05-19:
Yes I have done probe_calibrate and save_config but still I can see my first layer is not correct. I may have x twist and my bed is not perfect but I have some pretty good prints with stock firmware before flashing klipper (tried with different configs also) and if i exclude this issue I still have good prints but I'm pretty sure z offset is not applied on my prints ..
Is it a problem that I compiled .bin file myself and not flashed the one from your files?

bassamanator, 2023-05-19:
Compiling your own firmware is fine.

This doesn't look quite right to me:
```
## [probe]
## z_offset = 1.505
```
It should look like this (from my config):
```
#*# [probe]
#*# z_offset = 1.610
```
Do you have such a section in your `#*# <---------------------- SAVE_CONFIG ---------------------->` secion in your `printer.cfg`?

bladyle, 2023-05-19:
Yes i have that section and my values are exactly like yours with #*# at the front only the value is different.

bassamanator, 2023-05-19:
If that is the case, then `z_offset` is being applied, it doesn't require a manual load.

Did you see the `adjust your slicer` section?

bladyle, 2023-05-19:
Yes I'm using suggested slicer - super slicer with the bundle profile and The relevant macros for print start and end.

bassamanator, 2023-05-19:
That means your mesh is being loaded. While printing the first layer, depending on your mesh, you should see the screws rotating in some areas.

Closing as this is not an issue related to the config.

Feel free to create a discussion about this.

Closed 2023-05-19.

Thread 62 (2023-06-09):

Thoughts on enabling the SV06 Plus LCD?

ccatlett1984, 2023-06-09:
It has been mentioned on the Sovol support forum that it might be possible to enable the stock LCD screen for use with klipper.

bassamanator, 2023-06-09:
Yeah it's something that I want to do. Are you volunteering yourself as a tester/helper?

ccatlett1984, 2023-06-09:
I'm currently getting a Pi together and will be getting klipper installed shortly. I'm not a software dev, but have been doing IT consulting for 10+ years now, and would be happy to assist with testing/feedback.

NyoX01, 2023-06-10:
In my SV06 Plus FB group someone sent a link to a repo that enables the stock screen.
I'm completely new to Klipper and was asking about setting it up in the group, someone then put up this link.  I will post it here and maybe someone that has way more knowledge than I can try it out, or I will once I get enough nerve to actually try to klipperize my Plus.  OMG I'm so scared I'm going to screw something up...
https://github.com/fryc88/klipper-sv06plus-screen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
If this is not allowed, I'm sorry, just trying to help someone that may want that screen up and running.

bassamanator, 2023-06-10:
That is the work that I was going to pull into the `sv06-plus` branch. I find it could be a bit more user friendly. My concern at this point is that the klipper repo this work points to will never be integrated into klipper official, which is not necessarily a big deal.

In any case, this has been on my todo list for well over a month and remains as such at this point. Hope to get to it eventually.

NyoX01, 2023-06-10:
So Bassamanator, you are a legend! I thank you (like so many before me), for putting this together. But is there a fairly easy straightforward way to klipperize the Plus? Like an idiot's way lol? I've never really messed with Linux or Klipper and I even went as far as to download the write-up Rory had in our group. But after reading it several times there is terminology that I'm not familiar with. So once again, I'm terrified I'm going to screw something up...

bassamanator, 2023-06-10:
@NyoX01 Well, I would love to tell you that my instructions are idiotproof, but I know from experience that an idiot will always prove you wrong 🤣.

I want you to go read the full [documentation](https://github.com/bassamanator/Sovol-SV06-firmware/tree/sv06-plus) on the sv06-plus branch, let me know when you're done, and then I'll say more. It's about a 6-minute read.

NyoX01, 2023-06-10:
I went over the instructions several times, and printed them out so I could reference them as needed :)  I also sent you a message so we don't take up precious space on here.

bassamanator, 2023-06-10:
@NyoX01 Don't worry about space, and great!

So now that you've read the docs, I can tell you it's very difficult to 'brick' these boards (render them useless). If you start on this klipper path, and decide it's not for you half way through, you can always flash marlin back and be good to go again.

Just follow the instructions step by step, don't skip anything, and you'll be fine. Feel free to create a discussion if there are issues, I've walked many users through this process.

RandomSpaceship, 2023-06-12:
I've gone through the mods, and got the screen working. Most features work, but as noted in the repo, mesh leveling doesn't - in fact, it and all the other level commands crash Klipper!
If I have time, I might see if I can fix it, but no guarantees.

RandomSpaceship, 2023-06-12:
It works, but attempting to home the printer from the touchscreen doesn't. Once it starts an X/Y home the Klipper service on the Pi immediately crashes. Mesh leveling also immediately crashes, possibly due to attempting to home first. Outside of that, everything works as expected. Homing from the Mainsail interface or uploaded g-code works fine.

bassamanator, 2023-06-13:
@RandomSpaceship Interesting. I'm glad I haven't invested time in pulling in those changes. Curious, have you pointed mainsail to the [gbkwiatt](https://github.com/gbkwiatt/klipper) repo?

RandomSpaceship, 2023-06-13:
Correction: Klipper's not crashing, the printer firmware is. I didn't read the error properly.

Anyway, since I discovered that, I uploaded the `firmware5.bin` file from the repo (I built it myself before). It now works perfectly after a restart - even mesh bed leveling. There are still graphical issues (text boxes not properly aligned), but I can live with that. I haven't tried mechanical Z align since it's not great and I've aligned it manually.

ChrSch84, 2023-06-14:
@bassamanator Hello is there a "how to" or so to test it with the display. Your Klipper Konfig is working here @ 06 Plus but at the Moment without display.

Thanks for the hard work.

RandomSpaceship, 2023-06-14:
Yet Another Update: Homing crashes with the `firmware5.bin`! It seems inconsistent as to when it does or doesn't home. I don't have the time right now to run more tests and work out what exactly is happening, but it's worth noting.

bassamanator, 2023-06-14:
@ChrSch84 Well these are 2 separate entities, this repo and `fryc88's` guide to get the screen working. If you already have the OSSKC working on your Plus, you could go through the guide to try and get the screen working. Those encountering issues, @RandomSpaceship, should report the issues on those 2 repos, and hopefully get them fixed.

ccatlett1984, 2023-06-18:
I have the screen enabled, and most things seem to be working on my Plus.

bassamanator, 2023-06-18:
@ccatlett1984 Glad to hear it. I'm going to keep this issue open. Will call on you if/when I work on this.

Quick question: you are point to the [gbkwiatt](https://github.com/gbkwiatt/klipper) branch to make all this work?

ccatlett1984, 2023-06-19:
Correct, I set the gbkwiatt repo in KIAUH and installed everything through there.

fryc88, 2023-06-23:
> It works, but attempting to home the printer from the touchscreen doesn't. Once it starts an X/Y home the Klipper service on the Pi immediately crashes. Mesh leveling also immediately crashes, possibly due to attempting to home first. Outside of that, everything works as expected. Homing from the Mainsail interface or uploaded g-code works fine.

There's something to do with senseless homing & calling home for x y and z separately via the screen, I haven't had time to go that deep with it, but to be fair, who's doing mesh or homing via screen?
I had this up and running for ~6-7 months now on my SV01pro and homing issues shows up less often there, I'd say occasionally.
And no, it's not immediately crashing, it stops when it reaches the point of virtual end stops for some weird reason...
I'm using this only for basic stuff like adjusting offset, temps, etc. while printing, also, I'm happy anyway about having possibility to do so, instead of having a blank screen. Because of it's construction it will NEVER work as a proper klipperscreen, and original author of it (which is not gbkwiat, gbkwiat helped a lot to get it working on sovol screen and he set up that branch to auto merge with main klipper branch) has abandoned it completely.
Recently we've managed to sort max heating temps in the screen, because originally it was -15 degrees from temps set in the printers firmware, just FYI ;)

Closed 2023-07-30.

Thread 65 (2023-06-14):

Q: How to config for cooler stepper motors?

bladyle, 2023-06-14:
Hi, I'm running your config file without a problem but I have noticed that my stepper motors run hotter that stock firmware. What is the proper way to config them even if I have to sacrifice little bit of performance.

RandomSpaceship, 2023-06-14:
Run lower currents. In `printer.cfg`, under `[tmc2209 stepper_AXIS]`, there's a `run_current` variable. This is measured in amps delivered to the motors. Dropping it will reduce how much power gets sent to the motors, and therefore how much power is heating them.

However, IIRC the base Klipper config is the same as stock. If you're using print profiles with higher acceleration, that means that the motors need to make more force to move the axes around. As such, they might be getting _closer_ to their maximum current (they might not have been running at it before).

So, to keep them cool, you have two options: Reduce acceleration and reduce the current. However, since there isn't any fancy electronics in them, you can actually run them to be uncomfortably hot. If you can't touch them at all, that's too hot, but they can get surprisingly warm safely.

bladyle, 2023-06-14:
Yes I have just found my screenshots from stock firmware and compared the current there, just to confirm it's the same as you have wrote. I have occasionally run higher acceleration prints but not always and they are hotter even with slower prints. I'm sure they are still in  safe zone but want to try to reduce temp if it's possible. Do you know if reducing the microstep value will help lower the temp ?

RandomSpaceship, 2023-06-14:
I'm not sure, it's not something that I've looked into. I think it's exposed in the advanced settings menu in the stock firmware if you want to load that and compare it. Have you loaded the same g-code (or as close as you can get - same jerk/acceleration/speed settings) in both the stock and Klipper firmwares, and measured the motor temps? I find it very odd that the same print settings and motor configuration settings would make the motors hotter. However, if you still think they're running hot after whatever changes you make, motor heatsinks aren't very expensive on Aliexpress.

bassamanator, 2023-06-14:
@bladyle These motors can get as hot as 125C and be fine. They shouldn't be getting anywhere near that, however. Reducing microsteps shouldn't play a role here, but you could try it I suppose: 16, 32, 64, 128, and even 256 are valid values. It would help if you could take actual temperature readings, motors shouldn't be hitting the 60C mark.

In any case, feel free to keep reducing `run_current` until you start skipping steps.

Closed 2023-06-17.

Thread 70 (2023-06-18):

Fan controll of the controllboard fan

Remleyfpv, 2023-06-18:
I dont know if it is possible but would be cool if the controll board fan is controlled by the MCU temp of the STM. But I cant find what PIN this fan would be. The pin header is right next to a controllable fan(part cooling fan) so that leaves me to belive that it is a controllable fan output not just a 24V port.

bassamanator, 2023-06-18:
>The pin header is right next to a controllable fan(part cooling fan) so that leaves me to belive that it is a controllable fan output not just a 24V port.

Unfortunately, that is not the case. Not possible via software/config from what I've seen, and I've looked into this quite a bit.

Do contribute by creating a PR if you find a solution.

Remleyfpv, 2023-06-18:
oke and just to make sure: is yours turned of always to? or is mine just broken?

bassamanator, 2023-06-18:
Everyone's hotend cooling fan is always turned on for the SV06/Plus. It's not a controllable fan.

bassamanator, 2023-06-18:
Sorry, the motherboard fan turns on when the TMC drivers come into play, I assume. I say 'I assume' because I haven't found the pin config for it, nor does it listed in the official Marlin source code. What I do know that the motherboard fan turns on *only* when I start printing.

bassamanator, 2023-06-18:
[Here's](https://forum-drucktipps3d-de.translate.goog/forum/board/42-sovol/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) a forum that contains a lot of information, however, I have not found any of controlling 2 or the 3 fans, only the part cooling fan is controllable. It's in German but that link is running through google translate.

Closed 2023-06-18.

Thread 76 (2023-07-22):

Draw Purge Line[BUG]

Chewyyy, 2023-07-22:
**Describe the bug**
A clear and concise description of what the bug is.

**To Reproduce**
Steps to reproduce the behavior:
1. Start a Print
2. Print doesn't draw purge line
3. If you try and run draw_purge_line alone, it gives error "Error evaluating 'gcode_macro draw_purge_line:gcode': ZeroDivisionError: float division by zero"

**Expected behavior**
Drawing of a purge line before prints begin

**Screenshots**
If applicable, add screenshots to help explain your problem.

**What kind of device are you using to host Klipper?**
 - RPi 4B, up to date as of 07/22/2023

**How did you install Klipper?**
 - Mainsail

**Additional context**
No other macros being run other than your package

bassamanator, 2023-07-22:
There is no draw_purge_line macro included in this config. Please read about  purge_line macro in the docs.

Chewyyy, 2023-07-23:
You are absolutely right and I am an idiot.  Sorry!!!

Closed 2023-07-22.

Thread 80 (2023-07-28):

Add [z_tilt] config

chrisngobanh, 2023-07-28:
Just wondering why we have a [screws_tilt_adjust] but not a [z_tilt] config. Shouldn't it be the other way around for the SV06?

bassamanator, 2023-07-28:
This printer has 2 z stepper motors connected to the same stepper driver, meaning that the motors cannot work independently of each other. So `z_tilt` doesn't help us.

`screws_tilt_adjust` allows those of us who have done the silicon spacer mod to fine tune the tilt, if any, of our beds.

chrisngobanh, 2023-07-29:
Thanks for the info. I assumed that z_tilt was a manual process that I could use to adjust my lead screws, but I guess I could just create a separate macro for it.

Closed 2023-07-29.

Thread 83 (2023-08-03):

[BUG] Screws_Tilt_Adjust coordinates to nozzle instead of probe

race85com, 2023-08-03:
Current values in Screws_Tilt_Adjust reffer to position of screws to nozzle coordinates - not probe to screws coordinates. As a result, probing during SCREWS_TILT_CALCULATE is moved by offset of the probe, resulting in incorrect calculation.

I would suggest to change the config.cfg to these values, so that probe hits screws coordinates during SCREWS_TILT_CALCULATE

[screws_tilt_adjust]
screw1: 84.5, 136.5
screw1_name: center
screw2: 0, 51
screw2_name: front left
screw3: 170, 51
screw3_name: front right
screw4: 170, 221
screw4_name: back right
screw5: 0, 221
screw5_name: back left
speed: 60
horizontal_move_z: 10
screw_thread: CCW-M4

bassamanator, 2023-08-03:
This is pulled from [master](https://github.com/bassamanator/Sovol-SV06-firmware/blob/fea7a35c3af5aae0470c55aa9b0f2c119a4276c1/printer.cfg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):
```
[screws_tilt_adjust]
screw1_name: center
screw1: 84.50, 135
screw2_name: front left
screw2: 0, 51
screw3_name: front right
screw3: 169.75, 51
screw4_name: back right
screw4: 169.75, 221
screw5_name: back left
screw5: 0, 221
horizontal_move_z: 10
screw_thread: CCW-M4
```

Our two `screws_tilt_adjust` sections deviate by 1-2mm from what I see. Perfectly normal to have such a variance between the same model of printers at this price range.

Am I missing something here?

race85com, 2023-08-03:
I did not have the updated version of the master, now I see you have done a correction in the config a month ago, sorry for the confusion

bassamanator, 2023-08-03:
No worries my friend.

There's a pinned discussion explaining the update process. I suspect that you're a git user so it will be straight forward for you.

Feel free to open other issues! Best!

Closed 2023-08-03.

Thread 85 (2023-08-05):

Possible optimization on bed heating when close to target temperature?

Nukle0n, 2023-08-05:
Maybe this is a general Klipper thing but I figured I'd ask here since i'm using your config (thank you for making these by the way)

Sometimes when I've cancelled a print to quickly change something an then started it again, the temperature of the build plate has only fallen very little, like under 1 degrees celcius. But it still takes ages for it to get back up to the full 60 or 80, as if the printer is extremely scared of going slightly over, so it only heats extremely little, this means it will take 5 minutes for the printer to go from 59.4 to 60c. I've done PID tuning again to try and see why this could be, but it doesn't seem to help, it seems maybe the automatic parameters for calculating how to heat up the bed aren't optimal for when already close to the target temp?

bassamanator, 2023-08-05:
I've had a similar experience, and it's quite annoying. This is related to Klipper, not to this config.

Replace the following in your `cfgs/misc-macros.cfg`:
```
[gcode_macro M190]
rename_existing: M99190
gcode:
    #Parameters
    {% set s = params.S|float %}

    M140 {% for p in params %}{'%s%s' % (p, params[p])}{% endfor %}   ; Set bed temp
    {% if s != 0 %}
        TEMPERATURE_WAIT SENSOR=heater_bed MINIMUM={s-1} MAXIMUM={s+1}  ; Wait for bed temp (within 1 degree)
    {% endif %}
```

The `s-1` in `MINIMUM={s-1}` is saying that the minimum temp can be *under by 1 degree* of the *requested* temperature. Caveat, this will apply to all bed temperature settings, ie, every time you set a bed temperature.

Another caveat, this is just a 'hack', it is an attempt at compensating for a larger issue. Please create an issue here https://github.com/Klipper3d/klipper/issues.

bassamanator, 2023-08-05:
Also please let me know if this worked.

Nukle0n, 2023-08-05:
Thank you for the quick response, I'll try and put it into my config, not sure when it'll happen next but I'll try and remember to get back to you.

Sadly it appears you cannot make a github issue for Klipper, the "new issue" link gives you 3 options which are respectively reading their documentation, posting on their forum, or joining their Discord server.

bassamanator, 2023-08-05:
Sounds good. I'll try to talk to klipper guys/post on their forum.

Feel free to re-open issue!

Nukle0n, 2023-08-07:
user "why_me" recommended
```
[gcode_macro M190]
variable_temp_window: 5
variable_temp_boost: 10
rename_existing: M99190
gcode:
  #Parameters
  {% set set_temp = params.S|float %}
  {% set current_temp = printer.heater_bed.temperature %}
  {% set boost_temp = [set_temp + temp_boost, printer.configfile.settings.heater_bed.max_temp]|min %}
  {% set diff = set_temp - current_temp %}
  # safety
  {% if set_temp > printer.configfile.settings.heater_bed.max_temp %} { action_raise_error("ERROR: Bed temperature was set above bed limits") }{% endif %}

  {% if diff > 0 and diff < temp_window %} # only when heating up and close to target temperature
    M140 S{boost_temp}
    {% set temp_max = boost_temp %}
  {% else %}
    M140 S{set_temp}
    {% set temp_max = set_temp %}
  {% endif %}
  {% if set_temp != 0 %}
    TEMPERATURE_WAIT SENSOR=heater_bed MINIMUM={set_temp-1} MAXIMUM={temp_max + 5}  ; Wait for bed temp (within 1 degree)
  {% endif %}
  M140 S{set_temp}
```

Which seems to work decently,  making it start 1 degree short. with the KAMP bed levelling it evens out to the target for the most part anyway.

Closed 2023-08-05.

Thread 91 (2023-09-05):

[BUG] Klipper crashes/turns off after setting hotend temperature after M600/filament change

RedTheKitsune, 2023-09-05:
**Describe the bug**
On Sovol SV06 Plus, printer turns off after setting hotend temperature after M600/filament change gcode.

**To Reproduce**
Steps to reproduce the behavior:
1. Add M600 gcode on any layer
2. Wait for printer to execute it (move printhead forward)
3. Hotend temperature will be set to 0C
4. Set hotend temperature to anything
5. After like 5s printer will shutdown

**Expected behavior**
Not reset hotend temperature after M600/filament change gcode or fix the crash caused by setting hotend temperature.

**What kind of device are you using to host Klipper?**
 - OS: Odroid XU4

**How did you install Klipper?**
 - KIAUH

bassamanator, 2023-09-05:
This has nothing to do with the OSS config because I use filament change all the time. And the SV06 (me) and the Plus (you) share the same PCBs, so our experiences should be the same. The difference here is our operating systems, therefore this is an Odroid XU4 issue.

I'll have a quick look at the logs for you before I close this issue though, attach them here.

Also, are you up to date with this repo?

RedTheKitsune, 2023-09-06:
Soo I think this was caused by faulty USB cable or SBC USB port.
Found it because after updating config to the latest one, printer got randomly disconnected during homing procedure, so 100% it was an hardware issue.

Closed 2023-09-06.

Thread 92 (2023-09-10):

[BUG] Absolute / Relative mode

Regulate3772, 2023-09-10:
**Describe the bug**
I am not sure if I'm the only one with this problem but after quite a long research I want to share my path.

In the macros it seems that the extruder is supposed to work in absolute mode but in the linked slicer settings it is set to relative mode. This caused my prints to fail.

In the macro file, you define in which mode the extruder moves are calculated. You used
M82                                     ; Absolute extrusion mode

Yet in the slicer profiles (both superslicer and prusa), they use relative mode under: Printer Settings - General - Advanced - Use relative E - distances.
When working with your macros, this box needs to be unchecked or this error shows up in mainsail which cancels the print:
"Move exceeds maximum extrusion (4.357mm^2 vs 0.640mm^2)"

There is an explanation about absolute / relative mode here:
https://klipper.discourse.group/t/problem-move-exceeds-maximum-extrusion/3941/6

So either the macros needs to be changed to relative mode, or there should be a comment when linking the slicer profiles that the box needs to be unchecked to match the macros.

If I'm wrong or messed up my settings myself, I'm sorry.

**How did you install Klipper?**
 - KIAUH

bassamanator, 2023-09-10:
Thanks for creating this issue! I'll try to reproduce it on my end with a fresh OSS install.

A few quick questions:
- your printer model?
- when did you download this configuration? I just want to make sure that your local copy is up to date with this repo.

Regulate3772, 2023-09-10:
My model is Sovol SV06 Plus and I installed klipper (and your configs) about a month ago.

The print failiure comes only in some prints, it's more about the interaction of the slicer config and the macro file. It works perfectly fine when using the M82 in the macro as it is (absolute) instead of M83 (relative) if the described box is unchecked in the slicer.

I also know how it came to the mismatch.
Looking at Ellis changelog at https://github.com/AndrewEllis93/Ellis-SuperSlicer-Profiles
you can find:

> 2022-04-14:
> use_relative_e_distances back to enabled.
> Some people had M83 in their PRINT_START macros which didn't agree with this.

This means, about a year ago he changed the profile to relative mode while in your macro you use M82 (absolute) which causes errors at some prints.
In my opinion absolute is the better option. Yet, maybe you want to include in your description that you have to uncheck the box in prusa / superslicer for it to work with the macros.

bassamanator, 2023-09-11:
Having trouble reproducing.

Are you able to 'crash on demand'?

When you send a print like this:
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
it crashes?

Then when you just uncheck:
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
it prints just fine?

Regulate3772, 2023-09-11:
Exactly, both in prusaslicer and superslicer. It happens on very tall prints since the flow is calculated is not correct. Mostly on the second layer.

Besides reproducing: it is still fully possible that I messed up another setting although I reinstalled, downloaded and tested again. But other than that: it seems like you did program the start print code in absolute mode, right? You even commented it the macro file that it uses absolutes. So the slicer settings have to be matched to the macro file, doesn't it? Just in a programming way. The box in the slicer is exactly for that: to match it the start print, pause, filament change ect. (All in absolutes in the macro file)

bassamanator, 2023-09-13:
Unable to reproduce. Added note about this to discussion#13. Thanks.

Closed 2023-09-13.

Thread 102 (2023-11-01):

Filament sensor freezes klipper[BUG]

Trilis29, 2023-11-01:
When filament runout sensor detects runout my printer just freezes and is unresponsive, is it correct hehaviour?

bassamanator, 2023-11-01:
That's not the expected behavior. Check the FAQ section.

Trilis29, 2023-11-01:
I have checkeded FAQ also checked wires connected correctly to PCB, when there is no filament, I can see near mainboard led light goes out at SV06, like something is shorting... or maybe I have bad schematics of this sensor and need to swap something

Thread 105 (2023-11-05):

[FIX for known issue] Including `mcu_temp` temperature section **no longer** crashes Klipper with newly compiled firmware.

Errandir-of-Gondolin, 2023-11-05:
I've recently installed Klipper on the SV06 (using KIAUH and the provided cfg files and firmware in this repository - Klipper install is on an OG RPi4). But I ran into the issue that when I added the mcu_temp readout in the cfg file, it would read as -409°C in Fluidd. That is way outside the limits (including those of the physical world), causing the printer to shut down. My other 2 printers (not SV06), that run from the same RPi4, did not have this issue.

Rebooting Klipper and/or the printer didn't change anything. Only commenting out the mcu_temp section again would allow me to actually control the printer. The code I used to activate the mcu readout was:

```
[temperature_sensor mcu_temp]
sensor_type: temperature_mcu
sensor_mcu: mcu
min_temp: 0
max_temp: 100
```

Klipper, Moonraker and all OS packages were updated to the latest versions (on 05/11/2023). Based on a hunch from a friend, I manually compiled the firmware again via Klipper, flashed that, and it solved the problem. So any users using the 'old' firmware in the misc folder might see the same issues pop up if they add the mcu_temp section to the cfg file when using newer versions of Klipper.

I would suggest either removing the firmware file, or providing an update of the firmware, compatible with the latest version of Klipper.

Image below shows the readouts in Fluidd. The jumps to 0°C are at the timestamps of firmware restarts.
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

After compiling new firmware, using the settings below, and flashing it to the printer, all worked as normal again.
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

Output after flashing new firmware:
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

bassamanator, 2023-11-05:
I've known about this issue since the early days of this printer. Glad it's fixed! Will compile and test.

Thanks for reporting.

Errandir-of-Gondolin, 2023-11-06:
Another day, some more info. Sadly what I previously reported might not be an actual fix.

Context: today I resumed my calibration of the SV06. I started with the paper test, to set the z-offset. As soon as my nozzle dipped below 0 height (at which point the nozzle still didn't touch the bed), I got the same error: MCU temp out of range, back to -400°C. I recalled it was at the same exact moment in my calibration yesterday that this first popped up. So that got me thinking.

Sure enough, even reflashing the latest firmware didn't do anything. Probably because the probe was still at the same distance from the bed when rebooting the firmware, causing the same issue.

Temporary solution:
- commenting out the MCU_temp section of the printer.cfg file
- restarting firmware
- moving nozzle up
- uncommenting MCU_temp section
- restarting firmware ==> no more error

But as soon as you lower the printhead low enough (but still before the nozzle is close enough to the bed), the same error occurs and you need to start the process all over again.

I dialled in the z-offset via probe_calibrate, without the MCU_temp section in the cfg file, and I managed to set it to a value (default was 0, calibrated was around 1.5). I hoped that with a properly calibrated z-offset, the probe wouldn't be going too low for this to happen anymore, but sadly it is very repeatable. I don't even have to go to negative z-height values; lowering the nozzle to 1mm off the bed is enough for the error to trigger and shut everything down. The probe still is about 2.5mm above the bed at that point.

I have no idea how a seemingly probe-related issue can lead to unrealistic mcu temperature measurements, but here we are. For now I need to leave the mcu_temp section out of the config file to be able to proceed, but I'm concerned about the mcu not being monitored (including for too high temps). Not sure if there is actually any protection built into Klipper based on mcu temps going too high, but if there is, it might not function and hence increase the fire hazard of the printer.

bassamanator, 2023-11-06:
Ah what a pity. Thanks for the hard work looking into this. Please consider pasting links to where you asked about this and what info you found, in case someone wants to look into this in the future.

Closed 2023-11-06.

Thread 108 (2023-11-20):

Update guide & beep macro to work with sv06+ screen

frostius, 2023-11-20:
I flashed the screen to work with klipper and discovered that the beep macro does not work.  The M300 gcode is supported by the firmware, we just need to update the beep macro to match.

It would be cool if you could update the instructions to reflect that the beep does in fact work, and also update the `cfgs/misc-macros.cfg` beep macro to use the M300 gcode.

A couple of things to note:
- the firmware throws an error if duration > 255 and aborts the print.  Not cool.
- setting the frequency doesn't appear to do anything.  I haven't verified, but I'm assuming the screen only has a buzzer and not a piezo speaker.

This is a beep macro that includes error handling for duration values > 255 to avoid aborted prints

```shell
[gcode_macro BEEP]
description: BEEP I=3 DUR=200 FREQ=2000: Beep 3 times, for 200ms each, at 2kHz frequency.
gcode:
    # Parameters
    {% set i = params.I|default(1)|int %}           ; Iterations (number of times to beep).
    {% set dur = [params.DUR|default(100)|int,255] | min %}     ; Duration/wait of each beep in ms. Default 100ms.  Cap at 255 to avoid error
    {% set freq = params.FREQ|default(2000)|int %}  ; Frequency in Hz. Default 2kHz.

    {% for iteration in range(i|int) %}
        M300 P{dur} ;send to screen
        G4 P{dur}
    {% endfor %}
```

frostius, 2023-11-21:
Original non-klipper screen.

M300 is supported by the screen firmware per the firmware GitHub site

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

frostius, 2023-11-21:
Flashing the screen requires flashing an updated version of clipper to the
printer. I'm guessing M300 support is included in that branch?

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

bassamanator, 2023-11-21:
You're talking about the firmware from https://github.com/fryc88/klipper-sv06plus-screen?

If that is the case, then no, `M300` is not a built-in Klipper command, source: https://www.klipper3d.org/G-Codes.html?h=m11#g-code-commands. Must be something related to fryc88's fork of klipper, which is quite outdated at this point I notice now, unfortunately for plus owners.

frostius, 2023-11-21:
One more link deeper to the source:
https://github.com/Desuuuu/DGUS-reloaded-Klipper

------ Original Message ------
From "Bassam" ***@***.***>
To "bassamanator/Sovol-SV06-firmware"
***@***.***>
Cc "Matt Frost" ***@***.***>; "Author" ***@***.***>
Date 11/20/2023 7:31:25 PM
Subject Re: [bassamanator/Sovol-SV06-firmware] Update guide & beep macro
to work with sv06+ screen (Issue #108)

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

frostius, 2023-11-21:
I pulled from fryc88's last night which is currently on v0.11.  Version
0.12 was just released 2 weeks ago per
https://www.klipper3d.org/Releases.html#klipper-0110.  Per fryc88's
notes, the github is supposedly setup to auto-merge with the master
klipper branch - maybe gbkwiatt does testing before publishing.

What am I missing that makes you say this is "quite outdated"?  Is there
a version between 0.11 and 0.12?

------ Original Message ------
From "Bassam" ***@***.***>
To "bassamanator/Sovol-SV06-firmware"
***@***.***>
Cc "Matt Frost" ***@***.***>; "Author" ***@***.***>
Date 11/20/2023 7:31:25 PM
Subject Re: [bassamanator/Sovol-SV06-firmware] Update guide & beep macro
to work with sv06+ screen (Issue #108)

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

bassamanator, 2023-11-21:
Check the commit history, no recent commits:
- https://github.com/fryc88/klipper-sv06plus-screen/commits/main
- https://github.com/Desuuuu/DGUS-reloaded-Klipper/commits/master

bassamanator, 2023-11-21:
Actually, this is the 'fry' version of Klipper, https://github.com/gbkwiatt/klipper/commits/master, was updated recently.

In any case, not quite sure what to do since Klipper official doesn't support this command, and I have already created and maintain 4 branches on this repo alone. I think this kind of `special` info belongs in a discussion, will think about it later.

frostius, 2023-11-21:
Klipper firmware is pulled directly from
https://github.com/gbkwiatt/klipper

------ Original Message ------
From "Bassam" ***@***.***>
To "bassamanator/Sovol-SV06-firmware"
***@***.***>
Cc "Matt Frost" ***@***.***>; "Author" ***@***.***>
Date 11/20/2023 8:02:10 PM
Subject Re: [bassamanator/Sovol-SV06-firmware] Update guide & beep macro
to work with sv06+ screen (Issue #108)

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

frostius, 2023-11-21:
> In any case, not quite sure what to do since Klipper official doesn't support this command,

The `DGUS_PRINT_START` and `DGUS_PRINT_END` commands aren't klipper supported either.  If we want a working screen flashed with gbkwiatt's firmware, we're going to have to use instructions supported by that firmware.  In particular, M300 for the buzzer, and DGUS_PRINT_START/END to trigger screen updates.

If you don't want to support the screen integration, I'd be happy to create a github page that contains an updated version of `misc-macros.cfg` that work with the gbkwiatt screen firmware

bassamanator, 2023-11-22:
Let's think this through.

Where are `DGUS_PRINT_START` and `DGUS_PRINT_END` called `from`?

frostius, 2023-11-23:
> Where are DGUS_PRINT_START and DGUS_PRINT_END called from?
PRINT_START/END & CANCEL_PRINT, as per the instructions at https://github.com/fryc88/klipper-sv06plus-screen

bassamanator, 2023-11-23:
My friend, best is to actually fork this repo (tell it to copy all branches, then delete all branches except for `sv06-plus`).  Create a new branch, checked out from `sv06-plus`, along the lines of `sv06-plus-stock-screen`.

A fork will make it easier to stay up to date with this repo. I'm not sure how proficient you are with `git` so let me know if you need help with `git` commands.

bassamanator, 2023-11-25:
Closing this issue. Feel free to ping me.

Closed 2023-11-25.

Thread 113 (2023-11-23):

[BUG] KAMP doesnt seem to be purging.

iliyan61, 2023-11-23:
**Describe the bug**
There's no purge line when KAMP is enabled even with all the settings I can think of enabled.

**To Reproduce**
Steps to reproduce the behavior:
1. Send a print
2. wait for the printer to heat up
3. it starts the bed mesh
4. it finishes the bed mesh and starts printing with no purge

**Expected behavior**
I expect it to lay down a purge line.

**What printer are you using?**
- SV06,

**What kind of device are you using to host Klipper?**
 - OS: [Raspberry Pi]
 - Version: [4b+ on the latest debian]

**How did you install Klipper?**
 - KIAUH,

**Is your local copy of this configuration up to date?**
- Yes I just installed and set it up today.

bassamanator, 2023-11-23:
What slicer?

iliyan61, 2023-11-23:
Prusa Slicer. I had KAMP working on a previous install on klipper but i did a reinstall earlier today so I haven't touched pursaslicers code. The start G-Code is below I'm sure I've missed something but I'm not sure what it might be. Could you perhaps provide the steps to go through to re-enable it as it's not working across 2 printers and 2 separate machines.

'M104 S0 ; Stops PS/SS from sending temp waits separately
M140 S0
PRINT_START BED=[first_layer_bed_temperature] HOTEND=[first_layer_temperature[initial_extruder]]'

bassamanator, 2023-11-23:
You're missing `purge_line`, please see https://github.com/bassamanator/Sovol-SV06-firmware#adjust-your-slicer.

To use KAMP's line purge, please the KAMP faq section.

iliyan61, 2023-11-23:
I am fairly sure I have setup KAMP and it's purge line correctly going off what is written in your readme and I have gone through most of the configs related to it and enabled what seems necessary however it still doesn't work. I don't think I need to update my slicer G-Code as i already had it working with KAMP.

I followed your instructions anyway and it just lays a generic purge line. Could you please share the instructions to get KAMP purge line working with your config?

bassamanator, 2023-11-23:
Docs adjusted to add clarity: read kamp faq and adjust slicer sections again. Also pull repo.

Closed 2023-11-23.

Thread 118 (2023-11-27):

Error: Section 'axis_twist_compensation' is not a valid config section [BUG]

JoopVerdoorn, 2023-11-27:
**Describe the bug**
=======================
After installing Mainsail OS, emptying the ~/printer_data/config folder, using the git-method for retrieving and installing the SV06-plus configuration, determin the path of my printer and adding a line that in the printer.cfg of the MCU restarting the firmware gives this error in klippy.log:
`[filament_switch_sensor filament_sensor]
switch_pin = PA4
pause_on_runout = True
insert_gcode =
	{ action_respond_info("Insert Detected") }
runout_gcode =
	{ action_respond_info("Runout Detected") }
	CONDITIONAL_BEEP i=3 dur=300 freq=400
Extruder max_extrude_ratio=2.078758
Config error
Traceback (most recent call last):
  File "/home/pi/klipper/klippy/klippy.py", line 175, in _connect
    self._read_config()
  File "/home/pi/klipper/klippy/klippy.py", line 145, in _read_config
    pconfig.check_unused_options(config)
  File "/home/pi/klipper/klippy/configfile.py", line 299, in check_unused_options
    raise error("Section '%s' is not a valid config section"
configparser.Error: Section 'axis_twist_compensation' is not a valid config section
webhooks client 4130828688: New connection
webhooks client 4130828688: Client info {'program': 'Moonraker', 'version': 'v0.8.0-41-g348b7f5'}`

**To Reproduce**
Steps to reproduce the behavior:

1. Install Mainsail OS through the Raspberry pi imager
2. emptying the ~/printer_data/config folder
3. using the git-method for retrieving and installing the SV06-plus configuration
4. determin the path of my printer and adding a line that in the printer.cfg of the MCU
5. doing a FIRMWARE_RESTART

**Expected behavior**
Mainsail screen opens without an error

**Screenshots**
If applicable, add screenshots to help explain your problem.

**What printer are you using?**
SV06 Plus

**What kind of device are you using to host Klipper?**
Raspberry pi 4 with 4Gb RAM
- OS: Mainsail OS
- Version: 1.2.1

**How did you install Klipper?**
Included in Mainsail OS, which was installed using Raspberry pi Imager

- Manual install, KIAUH, MainsailOS, FluiddPi, etc.
None

**Is your local copy of this configuration up to date?**
My suspicion is that Mainsail OS comes with an older version of Klipper, where  =axis_twist_compensation= is not yet implemented

- This configuration changes all the time, when did you install it? Are you sure you're running the latest version?
This evening I installed everything

**What slicer are you using?**
- [ ] OrcaSlicer

**Are you using the config bundles from this repo?**
- [ ] Yes

**Did you [Adjust your slicer](https://github.com/bassamanator/Sovol-SV06-firmware#adjust-your-slicer)**?
Not relevant

**Additional context**
My suspicion is that Mainsail OS comes with an older version of Klipper, where  =axis_twist_compensation= is not yet implemented.
When I install KIAUH it says that version 0.11.0-205 of Klipper is installed, while 0.12.0-10 is the latest. Mainsail is version 2.5.1 while 2.8.0 is the latest. Moonraker is almost up to date.

After an update of Klipper, Mainsail and Moonraker through KIAUH everything works as expected.

So please add in the README.md after "Klipper must be installed on the host Raspberry Pi for everything to work. Easiest is to use a [MainsailOS](https://github.com/mainsail-crew/mainsail/releases/latest) image. Alternatively, you can install Fluidd or Mainsail via [KIAUH](https://github.com/th33xitus/kiauh)." that once needs to update MainsailOS through KIAUH

bassamanator, 2023-11-28:
Readme adjusted. Thanks.

Trilis29, 2023-11-28:
I don't see anything in readme about compensation

Closed 2023-11-28.

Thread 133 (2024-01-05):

Help with BTT PAD 7 Adxl345

Degenfoster, 2024-01-05:
Hey sorry i'm quite new to klipper and i just got it to work with my sv06+ with your guide, but i can't find how to use the ADXL 345 for input shaping with the BTT pad7, enabling adxl direct caused an error and klipper doesn't launch, please forgive me I'm really beginner at coding and stuff so i don't really understand it

MacBandito, 2024-01-05:
Did you follow the instructions in the Pad 7 manual?  You should have the BoardEnv.txt file thats installed when you follow the BTT instructions. You may have deleted it if you followed the Bassamanator instructions.  You need that file though to activate the correct setting.   I’ve pasted the instructions from the manual below.

Pad 7 Settings
Open the "BoardEnv.txt" configuration file, and set the following parameters:

spidev1_1: Enables the spidev1_1 to the system user space, allowing the Pad7's SPI port to connect to an ADXL345 accelerometer module.

Setting up ADXL345
As explained in "Pad 7 Settings" section, set the overlays to include spidev1_1.
After booting, the system user space should load spidev1.1. Add the following
configuration to the printer.cfg file to use the ADXL345:
[mcu CB1]
serial: /tmp/klipper_host_mcu
[adxl345]
cs_pin: CB1:None
spi_bus: spidev1.1
axes_map: z,y,-x # Modify according to the actual orientation of the ADXL345
installed on the printer.

Degenfoster, 2024-01-05:
I think you are right about  the config file being deleted, Is there a way to recover the file?

Degenfoster, 2024-01-05:
You are amazing! The config files of the pad 7 was already good, but the trick was the CB1 I kept following the wrong set of instructions for the CM4 board instead! So sorry rookie mistake but glad I finally could fix it!

MacBandito, 2024-01-05:
You’re welcome.  I’m very new to this too.

bassamanator, 2024-01-05:
@MacBandito Thanks for helping out the community! I've edited your original post for styling and to add sources. Please see if it still all makes sense or if I've blundered something.

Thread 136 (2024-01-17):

[BUG] Wont connect to printer

patchido, 2024-01-17:
**Describe the bug**
I can't get Klipper to connect to printer.

**To Reproduce**
I followed the guide, i do have a different username on my RPI3 but i changed the 2 files mentioned.
i installed Klipper on my RPI through KIUAH.

**What printer are you using?**

-SV06 Plus

**What kind of device are you using to host Klipper?**

- OS: [RPI3, flashed raspbian lite, the most updated one atm]
- Version: [raspberry pi os lite 64 bit released 2023 - 12 - 11]

**How did you install Klipper?**

- KIAUH

**Additional context**
I was able to use the same microsd card to flash back into stock firmware with no problem.

patchido, 2024-01-17:
so, i tried getting the usb by path instead of id, and that made it work somehow.

Closed 2024-01-17.

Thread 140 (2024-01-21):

[BUG] Homing in heated chamber sometimes causes false endstop trigger

GTreaper, 2024-01-21:
**Describe the bug**
After doing alot of printing inside a heated chamber printing ASA I stumbled upon a small hick up.
While homing it sometimes didn't move the X and Y axis(bed and tool head) all the way but triggered endstop causing it to move bed forward until it couldn't move anymore and continue to try moving it.

**To Reproduce**
Heat chamber to roughly 38c and up

**Expected behavior**
Home like it should

**What printer are you using?**

- SV06 Plus

**What kind of device are you using to host Klipper?
Pi 4

**Additional context**
To fix I lowered the value driver_SGTHRS in printer.cfg with - 2 on XY so far it hasn't happened but it's not a consistent issue.
It might need to be lowered more.

Wanted to post this incase any new user experience this issue. This could also happen if just the bed or tool head carriage are a bit to tight.
Repo owner may close this straight away if he doesn't feel like adding a note or two this was just intended for future users fault searching.

:)

bassamanator, 2024-01-21:
This is the nature of sensorless homing, the user might need to adjust related settings to have it work best with their unit, and, or, in their print environment.

Best.

Closed 2024-01-21.

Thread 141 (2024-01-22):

Add a mcu temperature sensor section

graccoon, 2024-01-22:
Fortunately, stm32 has an internal temperature sensor, which allows you to track frequent errors with its overheating (don't forget that in the standard configuration the MCU cooling fan is connected to the model cooling fan). In particular, the famous "timer too close" error has been haunting me for the last couple of weeks, and thanks to working with cooling and temperature tracking it was possible to eliminate MCU overheating.
And the proposed section is very simple:
```
[temperature_sensor mcu_temp].
sensor_type: temperature_mcu
min_temp: 0
max_temp: 100
```

graccoon, 2024-01-22:
I've found source of my code block:
https://klipper.discourse.group/t/stm32h743xx-mcu-temperature/5867/2

bassamanator, 2024-01-23:
This is nothing new; feel free to look through closed issues on this. The reason this section was *removed* from this config was because it doesn't play nicely with this motherboard.

It's very likely your issues are related to having added this section.

Closed 2024-01-23.

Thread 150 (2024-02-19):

[BUG] Layer shifting occurs at stock or near stock Klipper configs

LimesKey, 2024-02-19:
With the stock Klipper configs in this repository with 3000 Max Accel and 200 Max Velocity, I get severe layer shifting on my Sovol SV06.

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
This image was taken a few weeks ago and this is the most severe it has ever been, but usually it's a little better than this.

I have 2 SV06s both running Klipper on the same Raspberry Pi 4 4GB, layer shifting occurs on both on all axes except the Z (and extruder) I think. Even after increasing the X and Y motor currents by ~0.2 amps it still occurs, only after turning down the acceleration and velocity to 2000 and 100 respectively, does it cease.

I have not done any input shaping but I have made sure the rails and axes are well lubricated and that the bed cabling does not get caught or anything. Below are my printer configs for both printers.

[Cosmo-Printer.cfg.txt](https://github.com/bassamanator/Sovol-SV06-firmware/files/14337224/Cosmo-Printer.cfg.txt)
[Pepper-Printer.cfg.txt](https://github.com/bassamanator/Sovol-SV06-firmware/files/14337223/Pepper-Printer.cfg.txt)

bassamanator, 2024-02-19:
These limits are set to reasonable amounts. You are the first user mentioning this issue. I would suggest you check the initial steps section in the everything-sv06 repo.

Closed 2024-02-19.

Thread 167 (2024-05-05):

[BUG]  CANCEL_PRINT can collide with parts on the bed

Cornersruns, 2024-05-05:
**Describe the bug**
CACEL_PRINT raises the gantry slightly then moves the bed all the way back.  If there is a part at the front of the bed that is higher than the Z Height of the print the head collides with the part.  This is especially true when Print Sequence is by object.

**To Reproduce**
Steps to reproduce the behavior:

1. Start a print with Print Sequence by object, place a tall part at the front of the bed.
2. Once the tall part is printed and the printer has started on another item cancel Print
3. The print bed moves backward without the head being raised high enough to clear it.
4. The print head collides with the first printed part

**Expected behavior**
On cancel print, raise the print head but do not move the bed.

**What printer are you using?**

SV06 Plus,

**What kind of device are you using to host Klipper?**

Raspberry Pi

**How did you install Klipper?**

KIAUH

**Is your local copy of this configuration up to date?**
Yes

- This configuration changes all the time, when did you install it? Are you sure you're running the latest version?

**What slicer are you using?**

- [ ] PrusaSlicer
- [ ] SuperSlicer
- [ ] Cura
- [X] OrcaSlicer

**Are you using the config bundles from this repo?**

- [X ] Yes
- [ ] No

**Did you [Adjust your slicer](https://github.com/bassamanator/Sovol-SV06-firmware#adjust-your-slicer)**?

- [ X] Yes
- [ ] No

**Additional context**
Add any other context about the problem here.

bassamanator, 2024-05-06:
Before i think about this, how did you import the ps/ss config bundle into OS? Does OS have this functionality now?

Cornersruns, 2024-05-06:
I'm using Christian Vicks Orca Slicer Presets V1.5.5. With this start g-code:

`M104` S0 ; Stops PS/SS from sending temp waits separately
M140 S0
PRINT_START BED=[first_layer_bed_temperature] HOTEND=[first_layer_temperature[initial_extruder]]

`LINE_PURGE`

Klipper configs are purely yours with no other additions.

The cancel print is sent from klipper, Orca Slicer has a slicing setting of by Object so that each object, if multiple objects on a plate, is fully printed before the next object is started (instead of printing the whole plate layer by layey)

bassamanator, 2024-05-15:
Thanks for bringing this up. Unfortunately, I don't see how I can pull a previously printed parts height to include in the `print_end` macro, which is invoked during the cancellation process.

A `Known Issues` section has been added to the `README`; f27b569d0c16be6226833a225ea0535b65409d7c.

Closed 2024-05-15.

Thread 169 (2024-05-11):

SV06 SKR mini E3 V3 runout sensor

Astrolava, 2024-05-11:
I hooked up a filament runout sensor to the toolhead of my SV06, which uses an SKR Mini E3 V3, I'm very sure it's wired correctly.
My printer.cfg has the following:

[filament_switch_sensor filament_sensor]
switch_pin: !PA4 # "Pulled-high"
pause_on_runout: True
insert_gcode:
    M117 Insert Detected
    { action_respond_info("Insert Detected") }
runout_gcode:
    M117 Runout Detected
    { action_respond_info("Runout Detected") }
    CONDITIONAL_BEEP i=3 dur=300 freq=400

    I can see there's a "filament sensor" part on Klipper's dashboard now, but it says "empty" no matter if there's filament loaded or not.
    I don't seem to have any indication of a state change at all, and I'm wondering if I missed a step?
    It's a brand new filament runout sensor, but I don't even know how to test it to make sure the actual piece of hardware works.

The filament runout sensor is a cheap one off alieepress, so it's not at all impossible I got a faulty one.
I've tested the wire to confirm all 3 connections work.

Just to clarify the wiring.  On the toolhead, V is top, G is middle, S is bottom.
On the runout sensor, input side is V, middle is G, output side is S.

Any advice on how I might get this working?

jakebullet70, 2024-05-12:
I just setup one on an SKR 1.4 board on another printer. I used these docs.

https://www.klipper3d.org/G-Codes.html#filament_switch_sensor

I used 'QUERY_FILAMENT_SENSOR' command from the terminal until I had it working. For me it was the wrong pin.

Astrolava, 2024-05-12:
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

What pin did it end up being for you?
I have just finished testing pins PA-PF (0-15) - aside from the reserved and already used pins.
None of the pins detected the filament runout button being toggled.

I wonder if maybe there's an incorrect pin set somewhere which is occupying the pin for the sensor.
I noticed my screen's button doesn't work on PA15, but, it also didn't detect the filament runout.
I'm not too sure what to do now.

Astrolava, 2024-05-12:
These are the already occupied pins which I can't test for obvious reasons.  I wonder if one of these might be the actual probe pin, and if so, what that pin might otherwise be.

PA0 - [extruder] - sensor_pin
PA9 - [display] - encoder_pins
PA10 - [display] - encoder_pins
PA11 - reserved for USB
PA12 - reserved for USB
PA15 - [display] - click_pin (tested)

PB0 - [stepper_z] - step_pin
PB1 - [stepper_z] - enable_pin
PB2 - [stepper_y] - dir_pin
PB3 - [extruder] - step_pin
PB4 - [extruder] - dir_pin
PB5 - [output_pin beeper] pin
PB8 - [display] - cs_pin
PB9 - [display] - sclk_pin
PB10 - [stepper_y] - step_pin
PB11 - [stepper_y] - enable_pin
PB12 - [stepper_x] - dir_pin
PB13 - [stepper_x] - step_pin
PB14 - [stepper_x] - enable_pin
PB15 - [controller_fan electronic_enclosure_fan] - pin

PC0 - [tmc2209 stepper_x] - diag_pin
PC1 - [tmc2209 stepper_y] - diag_pin
PC4 - [heater_bed] - sensor_pin
PC5 - [stepper_z] - dir_pin
PC6 - [fan] pin
PC7 - [heater_fan hotend_fan] - pin
PC8 - [extruder] - heater_pin
PC9 - [heater_bed] - heater_pin
PC10 - [tmc2209 extruder] tx_pin
PC11 - [tmc2209 extruder] uart_pin
PC14 - [probe] - pin

PD1 - [extruder] - enable_pin
PD6 - [display] - sid_pin

PF0 - reserved for crystal?
PF1 - reserved for crystal?

Astrolava, 2024-05-12:
I guess another option here might be that the place where the P7 is plugged in requires more configuration.
If the port on the board, which I believe is labeled "DET (power detection?)" detects power being input, then it might require a source of power (3v or so?)  - but, if the DET doesn't also supply that power, then the filament sensor - which is just a button that joins two wires essentially - is just a dead wire.
Doesn't the output (DET) need to supply 3v to Vcc, then detect 3v in ground?  Is that how it works?

Right now, it seems that it's just a dead wire.  I couldn't get any reading on any of the pins of P7.

bassamanator, 2024-05-12:
You need to uncomment the filament sensor section in `printer.cfg`, as well as adjusting `misc-macros.cfg`. Please see [What are some settings that I can change?](https://github.com/bassamanator/Sovol-SV06-firmware/blob/skr-mini-e3-v3/README.md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). Read full docs before proceeding.

Ignore what it says on the dashboard. Start a print with no filament in the nozzle, but a piece of filament in the sensor. Remove the filament from the sensor to see if things are working as expected.

Astrolava, 2024-05-13:
> You need to uncomment the filament sensor section in `printer.cfg`, as well as adjusting `misc-macros.cfg`. Please see [What are some settings that I can change?](https://github.com/bassamanator/Sovol-SV06-firmware/blob/skr-mini-e3-v3/README.md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). Read full docs before proceeding.
>
> Ignore what it says on the dashboard. Start a print with no filament in the nozzle, but a piece of filament in the sensor. Remove the filament from the sensor to see if things are working as expected.

Am I still doing the pin PA4 ?

Astrolava, 2024-05-13:
So yeah, after testing and testing, it doesn't stop the print.  Doesn't pause it, doesn't beep, no indication at all that anything has changed.
It'll just keep printing without filament.

jakebullet70, 2024-05-13:
Had the same issue. You need to turn it on in the START gcode.

Astrolava, 2024-05-13:
> Had the same issue. You need to turn it on in the START gcode.

Thanks for the reply.  Umm, sorry I actually don't know how to turn it on.  Mind elaborating?

jakebullet70, 2024-05-13:
Yes that is right: SET_FILAMENT_SENSOR SENSOR=filament_sensor ENABLE=1

When setting up a filament sensor you do not need to print, you can use 'QUERY_FILAMENT_SENSOR' command and put filament in the sensor by hand, that tells you if you have the correct pin setup, once that is done and QUERY_FILAMENT_SENSOR works by telling when it has filament or not then you turn it on in your START gcode.

bassamanator, 2024-05-13:
> Am I still doing the pin PA4 ?

@Astrolava revert to whatever was already in `printer.cfg`.

Do not add `SET_FILAMENT_SENSOR SENSOR=filament_sensor ENABLE=1` but if you think you know better than the author of this config, go for it.

jakebullet70, 2024-05-14:
I sad that is what  had to do on an SKR 1.4 board. Did not work with out it.  Sorry,  I wll back out.

bassamanator, 2024-05-14:
@jakebullet70 No need to back out. The issue is that you'll have a hard time keeping up with any changes in this config. The only thing my users are required to do are to either uncomment/comment out a section, or change a 1 to a 0 or vice versa. No programming knowledge is *required*.

bassamanator, 2024-05-15:
Updated wiring diagram, printer.cfg and misc-macros.cfg. Pull new changes.

1. Take note of the wiring connecting to the SKR's `e0-stop`
2. Take note of how the filament sensor is connected to the hotend pcb.
3. Take note here: https://github.com/bassamanator/everything-sovol-sv06?tab=readme-ov-file#filament-sensor
4. Enable filament sensor via: https://github.com/bassamanator/Sovol-SV06-firmware/blob/skr-mini-e3-v3/README.md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

Can't simplify the process any further.

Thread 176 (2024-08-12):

KAMP has stopped  generating a mesh only in the area of printing

bladyle, 2024-08-12:
Hi, I'm using your klipper configuration since beginning and I'm very happy with it but since yesterday I noticed that when I send file to print and with activated KAMP, bed mesh is generated for the whole bed - not only for the object.
The only thing that I have modified to the system is that I casually run KIAUH  scripts for updates.

**What printer are you using?**

- SV06

**What kind of device are you using to host Klipper?**

- OS: old laptop
- Version: []

**How did you install Klipper?**

- Manual install, KIAUH

**Is your local copy of this configuration up to date?**

- This configuration changes all the time, when did you install it? Are you sure you're running the latest version?

**What slicer are you using?**

- [ ] OrcaSlicer

**Are you using the config bundles from this repo?**

- [ ] Yes
- [ ] No

**Did you [Adjust your slicer](https://github.com/bassamanator/Sovol-SV06-firmware#adjust-your-slicer)**?

- [ ] Yes
- [ ] No

bassamanator, 2024-08-12:
How did you enable KAMP? Is the configuration up to date with the repo?

bladyle, 2024-08-14:
I enable it from cfgs/misc-macros.cfg but I have seen now that are some new changes to repo.
I will update it and test again. Will report back when I test it.

bassamanator, 2024-08-14:
~Well, if you truly are up to date with the repo, you could try flashing a newer `klipper.bin`. This really shouldn't be necessary at all, but given the fact that~

Now that I think about it, it might be possible to determine if you're up to date with the repo. Run `_BED_MESH_CALIBRATE` in your klipper console (make sure your build plate is clear). What happens?

bladyle, 2024-08-15:
`_BED_MESH_CALIBRATE`   created new default mesh, although I noticed couple of `Probe samples exceed tolerance. Retrying...` when doing it

bassamanator, 2024-08-15:
The logic for the kamp routine is quite simple, even a non-coder can likely make sense of it,
```
    {% if kampEnabled == 0 %}
        BED_MESH_PROFILE LOAD=default                        ; NOTE if not using a mesh, comment out this line
        M104 S{hotendtemp}                                   ; set & don't wait for hotend temp
        G28 Z                                                ; final z homing
    {% else %}
        G28 Z                                                ; final z homing
        BED_MESH_CALIBRATE                                   ; KAMP mesh
        M104 S{hotendtemp}                                   ; set & don't wait for hotend temp
    {% endif %}
```
Given that Kamp works for me, I suspect that you either have not enable it, or your configuration isn't fully up to date.

I recommend you re-download the configuration (do the git method if you want to make your life easier with managing your config).

**Also, to clarify, KAMP was previously working for you?**

bladyle, 2024-08-15:
I have edited my last comment - it was my mistake...
I will use the post to ask you for another notification I receive now in klipper but didn't receive it before:

> Stepper driver warning: OTPW flag set
>
> The stepper driver 'stepper_z' has triggered the OTPW flag and may stop working if it gets any hotter. This is an indication of an over temperature condition. This can be caused by a too high current. Please check the stepper driver settings and cooling.

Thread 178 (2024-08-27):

[BUG]TEST_SPEED macro not working with latest Klipper release

smoothdog001, 2024-08-27:
**Describe the bug**
SET_VELOCITY_LIMIT ACCEL_TO_DECEL is depreciated with the latest version of Klipper and is now MINIMUM_CRUISE_RATIO. So the macro errors out where that is set.

Per:
https://www.klipper3d.org/G-Codes.html?h=minimum_cruise_ratio#set_velocity_limit

**To Reproduce**
Steps to reproduce the behavior:

Run TEST_SPEED macro

**Expected behavior**
Speed test completes

**Screenshots**
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

**What printer are you using?**

- SV06

**What kind of device are you using to host Klipper?**

BTT PAD7

**How did you install Klipper?**

KIAUH

**Is your local copy of this configuration up to date?**
Yes, confirmed in kiauh

- This configuration changes all the time, when did you install it? Are you sure you're running the latest version? Yes, just downloaded 2 days ago.

**What slicer are you using?**

N/A

**Are you using the config bundles from this repo?**

- [x ] Yes
- [ ] No

**Did you [Adjust your slicer](https://github.com/bassamanator/Sovol-SV06-firmware#adjust-your-slicer)**?

N/A

**Additional context**
Everything else has been running great! Thanks for this repo!

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
lincolnjohnson, 2024-08-27:
I had the same error, pulled the new test_speed.cfg, it works fine for me now.

bassamanator, 2024-08-29:
Tested and merged into all branches. Thanks all. 🙏🏻

Closed 2024-08-29.

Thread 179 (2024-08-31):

[BUG] Mainboard cooling fan and part cooling fan linked?

allylikesu, 2024-08-31:
**Describe the bug**
I'm not sure if this is an inherent flaw in the SV06's design, or a wiring flaw, or a firmware flaw, but it seems that the mainboard cooling fan is linked to the part cooling fan. I noticed this when I was printing without the part cooling fan on, and got stepper driver overheating warnings in Mainsail interface.

**To Reproduce**
Steps to reproduce the behavior:
Turn the fan off in Mainsail's dashboard. Examine both part cooling fan and mainboard fan for movement.
Turn fan to 100% and check on both again.

**Expected behavior**
Mainboard fan is statically set to 100%, or automatically set based on stepper driver temps

**What printer are you using?**

SV06 with stock fans and mainboard

**What kind of device are you using to host Klipper?**

Pi 4B running MainsailOS

**How did you install Klipper?**

MainsailOS

**Is your local copy of this configuration up to date?**

I installed it yesterday.

**What slicer are you using?**

PrusaSlicer

**Are you using the config bundles from this repo?**

Yes

**Did you [Adjust your slicer](https://github.com/bassamanator/Sovol-SV06-firmware#adjust-your-slicer)**?

I used the provided config bundles

**Additional context**
I can't inspect the mainboard right now, as I have a print running. I have a desk fan pointed at the mainboard enclosure, which seems to be doing the trick for now.

bassamanator, 2024-08-31:
By design? Who knows. Myself, I see it as a sign of neglect.

In any case, the behaviour that you observed is 'normal'.

The user @BeauSlim has a mod for the fans found [here](https://www.printables.com/@BeauSlim_355278).

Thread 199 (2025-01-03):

[BUG] MCU shutdwon: Timer too close

S1lv3rsur73r, 2025-01-03:
**Describe the bug**
Prints failing because of Error MCU shutdown: Timer too close

**To Reproduce**
Steps to reproduce the behavior:

Print anything

**Expected behavior**
No error occurs

**What printer are you using?**

- SV06

**What kind of device are you using to host Klipper?**

- Raspberry Pi 3A+

**How did you install Klipper?**

-MainsailOS

**Is your local copy of this configuration up to date?**

- Yes

**What slicer are you using?**

- [ ] OrcaSlicer

**Are you using the config bundles from this repo?**

-Yes

**Did you [Adjust your slicer](https://github.com/bassamanator/Sovol-SV06-firmware#adjust-your-slicer)**?

-Yes

**Additional context**
Too many microsteps. After lowering from 128 to 32 everything worked fine. Maybe change it or just add a comment behind the 128 to lower them when used with slower/older hardware.

bassamanator, 2025-01-03:
Valid point. Added to special considerations section. Thanks.

Closed 2025-01-03.

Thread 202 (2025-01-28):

[BUG]Beeper

Bandit-Designs, 2025-01-28:
**Describe the bug**
sv06 beeper is on all the time

**To Reproduce**
turn up beeper you can hear it

1. Go to 'beeper'
2. Click on 'beeper volum.'
3. Scroll down to 'beeper in desktop'
4. See error

**Expected behavior**
a screaming incredibly annoying beeeeeeeeeeeeeeeeeeeeeeeeeeepeeeeeeepeeeepeeeppee

**Screenshots**
If applicable, add screenshots to help explain your problem.

**What printer are you using?**

- SV06,.

**What kind of device are you using to host Klipper?** Laptop

- OS: [e.g. old laptop, PC, Raspberry Pi]
- Version: []laptop all up to date software

**How did you install Klipper?**with linix

- Manual install, KIAUH, MainsailOS, FluiddPi, etc. Mainsail

**Is your local copy of this configuration up to date?**as of tonight again

- This configuration changes all the time, when did you install it? Are you sure you're running the latest version?
always keepm,it up to date
**What slicer are you using?**
Prusa,
- [ *] PrusaSlicer
- [ ] SuperSlicer
- [ ] Cura
- [ ] OrcaSlicer

**Are you using the config bundles from this repo?**

- [* ] Yes
- [ ] No

**Did you [Adjust your slicer](https://github.com/bassamanator/Sovol-SV06-firmware#adjust-your-slicer)**?

- [** ] Yes
- [ ] No

**Additional context**
Add any other context about the problem here.
I need a beeper that doesn't drive my dogs to jump through windows

bassamanator, 2025-01-28:
Go over the **steps to reproduce** again please.

Bandit-Designs, 2025-01-28:
All I do is turn up the beeper on the klipper screen below the fan slider and the beep starts. I have to leave the beep volume turned off completely or my dogs go insane lol.
It’s been like this for awhile now. I’ve been searching for a fix for a long time. I just uploaded the latest from GitHub and it still does it
Sent from my iPad

On Jan 27, 2025, at 11:42 PM, Bassam ***@***.***> wrote:

Go over the steps to reproduce again please.

—
Reply to this email directly, view it on GitHub<https://github.com/bassamanator/Sovol-SV06-firmware/issues/202#issuecomment-2617832857>, or unsubscribe<https://github.com/notifications/unsubscribe-auth/BGOI5XMPS7MZA5FOTXYWXAT2M4DEFAVCNFSM6AAAAABV7SGOE2VHI2DSMVQWIX3LMV43OSLTON2WKQ3PNVWWK3TUHMZDMMJXHAZTEOBVG4>.
You are receiving this because you authored the thread.Message ID: ***@***.***>

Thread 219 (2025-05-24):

Sense resistor value

JavAstrologic, 2025-05-24:
Someone pointed out to me that the TMC2209 uses a 0.11 ohm resistor and questioned it in my printer.cfg.
Since I am using this printer.cfg, I figured I'd mention the issue here to see if it's intentional, a mistake, or if it simply doesn't matter.

bassamanator, 2025-05-24:
I've looked into this in the past, see `vfa` branch on this repo. I had heard similar, but couldn't find anything conclusive (maybe ask the person who told you this to provide a source?), so I merely looked at print quality, and couldn't find any differences in 0.110 vs 0.150.

I might switch my personal settings to 0.110 again to see if anything changes.

Would love to hear more on the matter.

JavAstrologic, 2025-05-25:
After doing lots of research, I've found multiple instances of 0.110, but nothing concretely conclusive.  The place I asked was the BTT discord, though the user who responded was not a moderator, and I can't tell whether or not they are a BTT employee.  If you'd like I can try to make contact with an employee who might be able to verify.  If I had a multimeter, I would just check the resistance on the board myself.

bassamanator, 2025-05-26:
If it's not too much trouble, please get any info that you can. It might not lead to anything, however, it will be here for people to look through.

One thing that I did want to mention is that all values, such as the `sense_resistor: 0.150` are pulled from the official marlin source code for this printer. There are exceptions such as `microsteps` and some `run_current` voltages, however.

bassamanator, 2025-05-27:
I did some testing with the different values again, and I see no difference in print quality.

JavAstrologic, 2025-06-16:
I actually use the SKR mini E3 V3, and mistakenly thought the TMC2209's would use the same sense resistor value on both the sv06 mainboard and skr mini.
Seems the SKR mini E3 V3 for sure has a 0.11 ohm, but the mainboard of SV06 wasn't super clear.  Thank you for clarifying.
I do wonder why the resistor values differ, but it seems to not even matter, I mean, as long as the results are the same.
I fried one of my sense resistors which is why I was looking into this in the first place, I thought maybe the value wasn't playing nice, but nope that resistor is fried entirely.
@bassamanator , I'm not sure if you want to reflect the SKR mini E3 V3's sense resistor value or not.

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

bassamanator, 2025-06-16:
@JavAstrologic It seems that you are correct as can be seen on this [page](https://bttwiki.com/TMC2209.html). Thanks for bringing this to my attention.

May I ask, are you using the skr-mini-e3-v3? Everything found on my repos has been tested, the skr branch has been tested by 2 different users because I don't use the skr (though I do own it, sitting in a box). Although a small change, I do prefer everything be tested before release to the public.

JavAstrologic, 2025-06-17:
> [@JavAstrologic](https://github.com/JavAstrologic) I've pushed the `sense_resistor` changes, please test if at all possible.

I've tested and all seems well.  I'd like to say I saw a positive change, but in honesty I can't tell the difference.

bassamanator, 2025-06-17:
Hehe yep. After much testing I've found it makes no difference in print quality.

I do wonder if it affects currents though. RE:

> Important Note About Stepper Motor Current
For the SKR-Mini-E3-V3.0, the run_current for x, y, z stepper motors has been reduced in the printer.cfg, because the standard current seems to make the steppers dangerously hot. You may have to increase the current, or if the motors are still too hot, you may have to decrease it.
https://github.com/bassamanator/Sovol-SV06-firmware/tree/skr-mini-e3-v3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

It would be interesting to see if your stepper motors run cooler, for example.

Closed 2025-06-28.

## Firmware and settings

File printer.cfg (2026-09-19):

# This file contains pin mappings for the stock Sovol SV06.
# 
# Find installation instructions at https://github.com/bassamanator/Sovol-SV06-firmware
# 
# See https://www.klipper3d.org/Config_Reference.html for configuration reference.

[include ./osskc.cfg]

[mcu]
# NOTE Obtain definition by "ls /dev/serial/by-id/*" or "ls /dev/serial/by-path/*"
serial: /dev/serial/by-path/platform-fd500000.pcie-pci-0000:01:00.0-usb-0:1.2:1.0-port0
restart_method: command

[printer]
kinematics: cartesian
max_velocity: 200
max_accel: 3000
max_z_velocity: 15
max_z_accel: 45
square_corner_velocity: 8.0

#####################################################################
#      X/Y/Z Stepper Settings
#####################################################################

[stepper_x]
step_pin: PC2
dir_pin: !PB9
enable_pin: !PC3
microsteps: 128
rotation_distance: 40
endstop_pin: tmc2209_stepper_x:virtual_endstop
position_endstop: 0
position_max: 223 # NOTE You can adjust this if you have more room
homing_speed: 40
homing_retract_dist: 0

[tmc2209 stepper_x]
uart_pin: PC1
run_current: 0.860
stealthchop_threshold: 0
interpolate: False
sense_resistor: 0.150
uart_address: 3
driver_SGTHRS: 81
diag_pin: PA5

[stepper_y]
step_pin: PB8
dir_pin: PB7
enable_pin: !PC3
microsteps: 128
rotation_distance: 40
endstop_pin: tmc2209_stepper_y:virtual_endstop
position_endstop: 0
position_max: 223 # NOTE You can adjust this if you have more room
homing_speed: 40
homing_retract_dist: 0

[tmc2209 stepper_y]
uart_pin: PC0
run_current: 0.900
stealthchop_threshold: 0
interpolate: False
sense_resistor: 0.150
uart_address: 3
driver_SGTHRS: 81
diag_pin: PA6

[stepper_z]
step_pin: PB6
dir_pin: !PB5
enable_pin: !PC3
microsteps: 128
rotation_distance: 4
endstop_pin: probe:z_virtual_endstop
position_min: -4
position_max: 258 # NOTE You can adjust this if you have more room
homing_speed: 5

[tmc2209 stepper_z]
uart_pin: PA15
run_current: 0.900
stealthchop_threshold: 0
interpolate: False
sense_resistor: 0.150
uart_address: 3
diag_pin: PA7

#####################################################################
#   Extruder
#####################################################################

[extruder]
step_pin: PB4
dir_pin: !PB3
enable_pin: !PC3
microsteps: 128
rotation_distance: 4.65 # NOTE Calibrate e-steps https://www.klipper3d.org/Rotation_Distance.html#calibrating-rotation_distance-on-extruders, https://github.com/bassamanator/everything-sovol-sv06/blob/main/howto.md#calibrate-esteps
nozzle_diameter: 0.400
filament_diameter: 1.750
heater_pin: PA1
sensor_type: EPCOS 100K B57560G104F
sensor_pin: PC5
control: pid
pid_kd: 86.991
pid_kp: 21.479
pid_ki: 1.326
min_temp: 0
max_temp: 300
max_extrude_only_distance: 150.0
max_extrude_cross_section: 5 # NOTE Needed for KAMP purge

[tmc2209 extruder]
uart_pin: PC14
run_current: 0.550
stealthchop_threshold: 0
interpolate: False
sense_resistor: 0.150
uart_address: 3

#####################################################################
#   Bed Heater
#####################################################################

[heater_bed]
heater_pin: PA2
sensor_type: EPCOS 100K B57560G104F
sensor_pin: PC4
control: pid
pid_kp: 64.440
pid_ki: 0.773
pid_kd: 1343.571
min_temp: 0
max_temp: 110

#####################################################################
#   Probe Related
#####################################################################

[probe]
pin: PB1
x_offset: 27
y_offset: -20
z_offset: 0
samples: 3
samples_result: median
samples_tolerance: 0.01
samples_tolerance_retries: 5

[safe_z_home]
home_xy_position: 84.50, 135 # NOTE The probe is at the center of the bed.
speed: 100.0
z_hop: 10
z_hop_speed: 15

[bed_mesh]
speed: 175
mesh_min: 27, 6 # probe as close to origin as possible while remaining fully on the bed
mesh_max: 222, 203 # (x.position_max - 1), (y.position_max - abs(y_offset)) ; probe as far as possible from the origin while remaining fully on the bed
probe_count: 5,5
algorithm: bicubic
fade_start: 1
fade_end: 10
fade_target: 0

[axis_twist_compensation]
calibrate_start_x: 27 # probe x coor at furthest left ; abs(x_offset)
calibrate_end_x: 195 # probe x coor at furthest right ; (x.position_max - abs(x_offset) - 1)
calibrate_y: 115

#####################################################################
#   Fans
#####################################################################

[fan]
pin: PA0

#####################################################################
#   Misc
#####################################################################

[display]
lcd_type: st7920
cs_pin: PB12
sclk_pin: PB13
sid_pin: PB15
encoder_pins: ^PB14, ^PB10
click_pin: ^!PB2

[bed_screws]
screw1_name: front left
screw1: 26.5, 31
screw2_name: front right
screw2: 196.75, 31
screw3_name: back right
screw3: 196.75, 201
screw4_name: back left
screw4: 26.5, 201

[screws_tilt_adjust]
screw1_name: center
screw1: 84.50, 135
screw2_name: front left
screw2: 0, 51
screw3_name: front right
screw3: 169.75, 51
screw4_name: back right
screw4: 169.75, 221
screw5_name: back left
screw5: 0, 221
horizontal_move_z: 10
screw_thread: CCW-M4

[output_pin beeper]
pin: PC6
value: 0
shutdown_value: 0
pwm: True
cycle_time: 0.0005 ; Default beeper tone in kHz. 1 / 0.0005 = 2000Hz (2kHz)

[filament_switch_sensor filament_sensor]
switch_pin: !PA4 # "Pulled-high"
pause_on_runout: True
insert_gcode:
    M117 Insert Detected
    { action_respond_info("Insert Detected") }
runout_gcode:
    M117 Runout Detected
    { action_respond_info("Runout Detected") }
    CONDITIONAL_BEEP i=3 dur=300 freq=400

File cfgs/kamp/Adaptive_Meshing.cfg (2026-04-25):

# # # Klipper Adaptive Meshing # # #

# Heads up! If you have any other BED_MESH_CALIBRATE macros defined elsewhere in your config, you will need to comment out / remove them for this to work. (Klicky/Euclid Probe)
# You will also need to be sure that [exclude_object] is defined in printer.cfg, and your slicer is labeling objects.
# This macro will parse information from objects in your gcode to define a min and max mesh area to probe, creating an adaptive mesh!
# This macro will not increase probe_count values in your [bed_mesh] config. If you want richer meshes, be sure to increase probe_count. We recommend at least 5,5.

# NOTE ignore commments about the name of klipper macro BED_MESH_CALIBRATE -bassamanator

[gcode_macro KAMP_BED_MESH_CALIBRATE]
gcode:

    {% set all_points = printer.exclude_object.objects | map(attribute='polygon') | sum(start=[]) %}                                # Gather all object points
    {% set bed_mesh_min = printer.configfile.settings.bed_mesh.mesh_min %}                                                          # Get bed mesh min from printer.cfg
    {% set bed_mesh_max = printer.configfile.settings.bed_mesh.mesh_max %}                                                          # Get bed mesh max from printer.cfg
    {% set probe_count = printer.configfile.settings.bed_mesh.probe_count %}                                                        # Get probe count from printer.cfg
    {% set kamp_settings = printer["gcode_macro _KAMP_Settings"] %}                                                                 # Pull variables from _KAMP_Settings
    {% set verbose_enable = kamp_settings.verbose_enable | abs %}                                                                   # Pull verbose setting from _KAMP_Settings
    {% set probe_dock_enable = kamp_settings.probe_dock_enable | abs %}                                                             # Pull probe dockable probe settings from _KAMP_Settings
    {% set attach_macro = kamp_settings.attach_macro | string %}                                                                    # Pull attach probe command from _KAMP_Settings
    {% set detach_macro = kamp_settings.detach_macro | string %}                                                                    # Pull detach probe command from _KAMP_Settings
    {% set mesh_margin = kamp_settings.mesh_margin | float %}                                                                       # Pull mesh margin setting from _KAMP_Settings
    {% set fuzz_amount = kamp_settings.fuzz_amount | float %}                                                                       # Pull fuzz amount setting from _KAMP_Settings
    {% set probe_count = probe_count if probe_count|length > 1 else probe_count * 2  %}                                             # If probe count is only a single number, convert it to 2. E.g. probe_count:7 = 7,7
    {% set max_probe_point_distance_x = ( bed_mesh_max[0] - bed_mesh_min[0] ) / (probe_count[0] - 1)  %}                            # Determine max probe point distance
    {% set max_probe_point_distance_y = ( bed_mesh_max[1] - bed_mesh_min[1] ) / (probe_count[1] - 1)  %}                            # Determine max probe point distance
    {% set x_min = all_points | map(attribute=0) | min | default(bed_mesh_min[0]) %}                                                # Set x_min from smallest object x point
    {% set y_min = all_points | map(attribute=1) | min | default(bed_mesh_min[1]) %}                                                # Set y_min from smallest object y point
    {% set x_max = all_points | map(attribute=0) | max | default(bed_mesh_max[0]) %}                                                # Set x_max from largest object x point
    {% set y_max = all_points | map(attribute=1) | max | default(bed_mesh_max[1]) %}                                                # Set y_max from largest object y point

    {% set fuzz_range = range((0) | int, (fuzz_amount * 100) | int + 1) %}                                                          # Set fuzz_range between 0 and fuzz_amount
    {% set adapted_x_min = x_min - mesh_margin - (fuzz_range | random / 100.0) %}                                                   # Adapt x_min to margin and fuzz constraints
    {% set adapted_y_min = y_min - mesh_margin - (fuzz_range | random / 100.0) %}                                                   # Adapt y_min to margin and fuzz constraints
    {% set adapted_x_max = x_max + mesh_margin + (fuzz_range | random / 100.0) %}                                                   # Adapt x_max to margin and fuzz constraints
    {% set adapted_y_max = y_max + mesh_margin + (fuzz_range | random / 100.0) %}                                                   # Adapt y_max to margin and fuzz constraints

    {% set adapted_x_min = [adapted_x_min , bed_mesh_min[0]] | max %}                                                               # Compare adjustments to defaults and choose max
    {% set adapted_y_min = [adapted_y_min , bed_mesh_min[1]] | max %}                                                               # Compare adjustments to defaults and choose max
    {% set adapted_x_max = [adapted_x_max , bed_mesh_max[0]] | min %}                                                               # Compare adjustments to defaults and choose min
    {% set adapted_y_max = [adapted_y_max , bed_mesh_max[1]] | min %}                                                               # Compare adjustments to defaults and choose min

    {% set points_x = (((adapted_x_max - adapted_x_min) / max_probe_point_distance_x) | round(method='ceil') | int) + 1 %}          # Define probe_count's x point count and round up
    {% set points_y = (((adapted_y_max - adapted_y_min) / max_probe_point_distance_y) | round(method='ceil') | int) + 1 %}          # Define probe_count's y point count and round up

    {% if (([points_x, points_y]|max) > 6) %}                                                                                       # 
        {% set algorithm = "bicubic" %}                                                                                             # 
        {% set min_points = 4 %}                                                                                                    # 
    {% else %}                                                                                                                      # Calculate if algorithm should be bicubic or lagrange
        {% set algorithm = "lagrange" %}                                                                                            # 
        {% set min_points = 3 %}                                                                                                    # 
    {% endif %}                                                                                                                     # 

    {% set points_x = [points_x , min_points]|max %}                                                                                # Set probe_count's x points to fit the calculated algorithm
    {% set points_y = [points_y , min_points]|max %}                                                                                # Set probe_count's y points to fit the calculated algorithm
    {% set points_x = [points_x , probe_count[0]]|min %}
    {% set points_y = [points_y , probe_count[1]]|min %}

    {% if verbose_enable == True %}                                                                                                 # If verbose is enabled, print information about KAMP's calculations
        {% if printer.exclude_object.objects != [] %}

            { action_respond_info( "Algorithm: {}.".format(                                                                              
                (algorithm),                                                                                                            
            )) }

            { action_respond_info("Default probe count: {},{}.".format(                                                                  
                (probe_count[0]),                                                                                                       
                (probe_count[1]),                                                                                                       
            )) }

            { action_respond_info("Adapted probe count: {},{}.".format(                                                                  
                (points_x),                                                                                                             
                (points_y),                                                                                                             
            )) }
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

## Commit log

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2022-12-26 Added adxl345 settings. Added z_hop to safe_z_home. Disabled stealthchop.
    [klipper-printer-sovol-sv06.cfg]
2022-12-26 Added source for gantry leveling. Added macros.cfg. Many minor adjustments to printer.cfg.
    [klipper-printer-sovol-sv06.cfg, macros.cfg, mechanical_level_tmc2209.cfg]
2022-12-26 Adjusted cancel_print. Added pause, resume, m600.
    [macros.cfg]
2022-12-26 Adjusted speed in purge_line.
    [macros.cfg]
2022-12-26 Added conditional homing macro.
    [macros.cfg]
2022-12-26 Added temperatures section in printer.cfg.
    [klipper-printer-sovol-sv06.cfg]
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2022-12-31 Moved test_speed macro to own file.
    [TEST_SPEED.cfg, klipper-printer-sovol-sv06.cfg, macros.cfg]
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2022-12-31 Update klipper-printer-sovol-sv06.cfg
    changed bed mesh from 5x5 to 10x10
    [klipper-printer-sovol-sv06.cfg]
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2023-01-01 Update klipper-printer-sovol-sv06.cfg
    set probe offset to correct values and modified min and max values for bed mesh accordingly.
    [klipper-printer-sovol-sv06.cfg]
2023-01-07 Renamed some .cfg files.
    [MECHANICAL_GANTRY_CALIBRATION.cfg, klipper-printer-sovol-sv06.cfg, macros.cfg]
2023-01-07 Moved macros to macros/.
    [MECHANICAL_GANTRY_CALIBRATION.cfg, PARKING.cfg, TEST_SPEED.cfg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]
2023-01-13 Added BED_MESH_PROFILE LOAD to PRINT_START.
    [macros.cfg]
2023-01-13 Fixed indentation in macros.cfg.
    [macros.cfg]
2023-01-13 More cleanup in macros.cfg.
    [macros.cfg]
2023-01-13 Implemented the use of PRE_PURGE_PRIME_LENGTH in purge_line and print_end macros.
    [macros.cfg]
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2023-01-22 Update klipper-printer-sovol-sv06.cfg
    changed x mesh_max to better fit the bed size
    [klipper-printer-sovol-sv06.cfg]
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2023-01-24 Adjusted probe: speed, samples, tolerance, retries.
    [klipper-printer-sovol-sv06.cfg]
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2023-01-26 Pulled in changes from main to fix probe_calibrate issue.
    [printer.cfg]
2023-01-26 Copy pasted original (roughly) to resolve OOR issue.
    [printer.cfg]
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2023-01-28 Adjusted PRINT_START to start heating hotbed and hotend at the same time.
    [macros.cfg]
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2023-02-01 Changed safe_z_home to 0, 223. Added relative ref index 20. Added loose z_offset.
    [printer.cfg]
2023-02-02 New settings working; a lot better. z_offset adjusted. New bed mesh.
    [printer.cfg]
2023-02-02 Adjusted master branch with safe limits, and notes, to accomodate beginner user.
    [TEST_SPEED.cfg, printer.cfg]
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2023-02-03 Fixed imports.
    [printer.cfg]
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2023-02-04 Removed mcu and rpi sections. Change max_temp extruder to 300.
    [printer.cfg]
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2023-02-04 Adjusted PURGE_LINE: raise nozzle higher at the end.
    [macros.cfg]
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2023-02-07 Adjusted MECHANICAL_GANTRY_CALIBRATION. Adjusted z position_max to 258 because of silicon screws.
    [MECHANICAL_GANTRY_CALIBRATION.cfg, printer.cfg]
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2023-02-07 New mesh. Added relative_reference_index to bed_mesh, adjusted safe_z_home accordingly.
    [printer.cfg]
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2023-02-09 New mesh, will not get better than this: 1.500 z_offset-best.
    [printer.cfg]
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2023-02-15 Adjusted G34: now will grind against top beam for 20mm.
    [MECHANICAL_GANTRY_CALIBRATION.cfg]
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2023-02-15 README.md contains full instructions. Added current SuperSlicer config bundle. printer.cfg adjusted: Z position_min, improved comments.
    [macros.cfg, printer.cfg]
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2023-02-22 New z_offset and mesh after new part cooler. Prev z_offset 1.515 was good.
    [printer.cfg]
2023-02-24 Set x, y, z microsteps to 64 to reduce whine.
    [printer.cfg]
2023-02-28 Deleted unnecessary files. NOTE: users need not pull these changes.
    [klipper-printer-sovol-sv06.cfg]
2023-02-28 NOTE: users SHOULD pull in these changes. Removed test_speed.cfg import; macro is not ready for use.
    [TEST_SPEED.cfg, printer.cfg]
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2023-03-08 Implemented TEMPERATURE_WAIT in macros. NOTE: users should pull these changes.
    [macros.cfg]
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2023-03-09 Change git clone style to use https / avoid permission error
    On a fresh raspberrypi, users may find it easier to just do:
    git clone -b master --single-branch https://github.com/bassamanator/Sovol-SV06-firmware.git .
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2023-03-12 ADJUST_FILAMENT_SENSOR_STATUS and conditional_beep fixed.
    [misc-macros.cfg]
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2023-03-12 Reversed filament sensor pin.
    [printer.cfg]
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2023-03-16 Remade this branch with latest changes from master.
    [MECHANICAL_GANTRY_CALIBRATION.cfg, misc-macros.cfg, printer.cfg]
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2023-04-02 Adjusted filament sensor to use action_respond_info for plus users.
    [printer.cfg]
2023-04-02 Purge_line macro adjusted to print at the front of the bed; printer agnostic. Print_end adjusted to use safer speed.
    [misc-macros.cfg]
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2023-04-02 Removed bed_screws locations from plus. Enabled filament sensor. Adjusted safe_z_home.
    [misc-macros.cfg, printer.cfg]
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2023-04-03 Reversed switch_pint in filament sensor pinout section based on facebook user feedback.
    [printer.cfg]
2023-04-04 Adjusted run_current for plus based on official sovol specs.
    [printer.cfg]
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2023-04-07 Adjusted PRINT_START sequence to save time, and to prevent oozing. Increased microsteps to 128, and added square_corner_velocity.
    [misc-macros.cfg, printer.cfg]
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2023-04-07 Added pause/runout/m600 to faq. Reduced speed in print_start.
    [misc-macros.cfg]
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2023-04-20 Add a minimum bed temperature of 0 degrees
    If the bed temperature is less than 2, the print job fails with an
    error message complaining about an invalid temperature. This happens,
    for instance, when printing ABS where the bed is not supposed to be
    heated.
    This change makes sure that the bed temperature cannot be negative.
    [misc-macros.cfg]
2023-04-21 Add config for 2 ADXL345 via RasPi pico
    This adds a configuration supporting two ADXL345 sensors at the same
    time though a Raspberry Pi pico.
    Resonance measurements for both the head and the bed can be done without
    having to change the sensors.
    [adxl-rpi-pico-2x.cfg, printer.cfg]
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2023-04-22 Avoid cooling down the extruder in PRINT_START
    The current `PRINT_START` macro heats the extruder to 150 degrees, then
    to 170, and finally to the target temperature. If the extruder is
    already hot, this unnecessarily cools it down and wastes time.
    This change only cools down the hotend if it's above the target
    temperature and then only to that temperature.
    If the extruder was colder than 150 degrees, this change maintains the
    current behaviour.
    [misc-macros.cfg]
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2023-05-11 Added sv06-plus build plate model, removed sv06 build plate.
    [SV06-buildPlate.stl, SV06Plus-buildPlate.stl]
2023-05-20 Pulled in print_start from personal: prints start with higher bed temp now, range 10C.
    [misc-macros.cfg]
2023-05-21 Pulled in print_start from master: prints start with higher bed temp now, range 10C.
    [misc-macros.cfg]
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2023-06-20 replaced manual PID/calibration steps with reusable macros
    [CALIBRATION.cfg, printer.cfg]
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2023-07-01 Cleanup in misc-macros.cfg. Adjusted calibration.cfg to work dynamically.
    [CALIBRATION.cfg, misc-macros.cfg]
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2023-09-07 Fix calibrate esteps link, and add accompanying everything-sv06 link. Adjust calibration.cfg to turn off print cooling fan after pid tune hotend.
    [CALIBRATION.cfg, printer.cfg]
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2023-11-23 Adjust kamp settings: include line_purge; adjust printer.cfg accordingly; adjust readme.md, slicer and kamp sections.
    [KAMP_Settings.cfg, printer.cfg]
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2024-08-29 Fix test_speed macro.
    [TEST_SPEED.cfg]
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2025-01-03 Add mcu timer too close error to special considerations.
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2025-07-21 Fix support settings for 0.6 nozzle; OS.
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2026-04-25 Adjust macro names: LINE_PURGE -> KAMP_LINE_PURGE, and undo name changes that KAMP brought with it.
    [Adaptive_Meshing.cfg, CALIBRATION.cfg, Line_Purge.cfg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]
